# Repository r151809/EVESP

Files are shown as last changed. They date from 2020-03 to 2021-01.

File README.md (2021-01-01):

# EVESP
ESP32 (Lolin32) based EV charge controller
Implement charging controller according to SAE J1772 (https://en.wikipedia.org/wiki/SAE_J1772) and relay driver.

Project maturity: just schematics (no testing nor SW yet)!

Only fixed cables are supported (no PP support).

Recidual current (AC+DC) protection is planned with https://deltrixchargers.com/wp-content/uploads/2019/10/WA-DS-015-RCM14-03-Rev-B.pdf
https://www.stegen.com/nl/ev-producten/126-residual-current-sensor.html

Three relays, one for each phase. This is inteded for cases when there is unsymmetrical load in the house, and you still want to charge the car (maybe there is another car charging in one phase already). Another usecase is cars that go to sleep when not charged, and while sleeping they do not accept pre heat commands from the cloud. My take for that would be charging with single phase with 6A current, instead of not charging at all, full 3-phase charging only when you really want to charge. Changing the phases on the fly might not be supported by cars, but that is easy to overcome by stopping the charge before switching on/off any phases.

Misc features:
4 local LEDs
8 IO for external LEDs or buttons
1 up to 12 V LED output for lighting up the charging cable dummy socket (where you keep the cable when it's not connected to car)  

Many ideas (component selection) of the schematic are taken from https://github.com/SmartEVSE/smartevse and from http://www.analogevse.xyz/AnalogEVSE-en.html. 

PWM generation and Wifi connectivity is handled with LoLin32-board:
https://wiki.wemos.cc/products:lolin32:lolin32
It's discontinued already, but you can still find them from ebay.
Pinout is here: https://arduino-projekte.info/wemos-lolin32/

Security:
SW cannot enable relay drivers unless RCM is happy and CP is connected to some load. So the design should be safe in case of forced disconnect and any ground leakage.

Manufacturing of the first PCB patch was done by Itead.cc with files in EVESP.zip.

## Copying
Feel free to copy anything I have added to this project. If it is not too much to ask, please let me know what you are doing (it's not mandatory) :). Also any bug's would be nice to know.

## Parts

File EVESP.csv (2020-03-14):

Id | Designator | Kotelo | Lukumäärä | Merkintä | Supplier and ref
1 | C21,C20,C19,C23,C22,C18,C17,C16,C13,C11,C15,C14,C10,C9,C8 | C_0805_2012Metric_Pad1.15x1.40mm_HandSolder | 15 | 100n
2 | C2,C12 | C_0805_2012Metric_Pad1.15x1.40mm_HandSolder | 2 | 10u
3 | R30,R23,R17 | R_0805_2012Metric_Pad1.15x1.40mm_HandSolder | 3 | 100k
4 | D13,D12,D11,D5,D4,D3,D2,D1 | SOT-23 | 8 | BAT54S
5 | H6,H5,H4,H3 | MountingHole_4.3mm_M4 | 4 | MountingHole
6 | D10,D9,D8,D7 | LED_2010_5025Metric_Pad1.52x2.65mm_HandSolder | 4 | LED
7 | R22,R15 | R_0805_2012Metric_Pad1.15x1.40mm_HandSolder | 2 | 1M
8 | J12,J11,J10,J1 | TerminalBlock_bornier-2_P5.08mm | 4 | Screw_Terminal_01x02
9 | U4,U3,U2 | SMDIP-6_W7.62mm | 3 | MOC3063M
10 | U5,U1 | SOIC-8_3.9x4.9mm_P1.27mm | 2 | LM7332
11 | R21,R40 | R_0805_2012Metric_Pad1.15x1.40mm_HandSolder | 2 | 47k
12 | R20,R19,R16,R9,R49,R13,R8,R6,R38,R42,R41,R39,R12,R7,R5,R4,R3,R34,R24,R10,R11,R2,R1 | R_0805_2012Metric_Pad1.15x1.40mm_HandSolder | 23 | 10k
13 | R18 | R_0805_2012Metric_Pad1.15x1.40mm_HandSolder | 1 | 6k8
14 | Q3,Q2,Q1 | SOT-23 | 3 | BC847
15 | J2 | Wago_734-136_1x06_P3.50mm_Vertical | 1 | Screw_Terminal_01x06
16 | R50,R48,R47,R46 | R_1206_3216Metric_Pad1.42x1.75mm_HandSolder | 4 | 470R
17 | R45,R44,R43,R14,R25 | R_0805_2012Metric_Pad1.15x1.40mm_HandSolder | 5 | 1k
18 | J9,J8 | Wago_734-133_1x03_P3.50mm_Vertical | 2 | Screw_Terminal_01x03
19 | J7 | PinHeader_1x20_P2.54mm_Vertical | 1 | Conn_01x20_Male
20 | J6 | PinHeader_1x20_P2.54mm_Vertical | 1 | Conn_01x20_Female
21 | J5 | PinHeader_1x16_P2.54mm_Vertical | 1 | Conn_01x16_Female
22 | J4 | PinHeader_1x16_P2.54mm_Vertical | 1 | Conn_01x16_Male
23 | D6 | D_SMA_Handsoldering | 1 | SMAJ13CA-13-F
24 | R29,R28,R27,R26,R37,R36,R35 | R_0805_2012Metric_Pad1.15x1.40mm_HandSolder | 7 | 470R
25 | RV3,RV2,RV1 | RV_Disc_D15.5mm_W6.8mm_P7.5mm | 3 | V275LA20AP
26 | PS3,PS2 | Converter_ACDC_MeanWell_IRM-02-xx_THT | 2 | IRM-02-12
27 | PS1 | Converter_ACDC_MeanWell_IRM-02-xx_THT | 1 | IRM-02-3.3
28 | J3 | JST_EH_B4B-EH-A_1x04_P2.50mm_Vertical | 1 | Conn_01x04
29 | F1 | Fuseholder_Cylinder-5x20mm_Stelvio-Kontek_PTF78_Horizontal_Open | 1 | 1.25A
30 | C3 | R_0805_2012Metric_Pad1.15x1.40mm_HandSolder | 1 | DNI 100n
31 | C7,C6,C5 | C_Radial_D6.3mm_H11.0mm_P2.50mm | 3 | 47u
32 | C4 | C_0805_2012Metric_Pad1.15x1.40mm_HandSolder | 1 | 270p

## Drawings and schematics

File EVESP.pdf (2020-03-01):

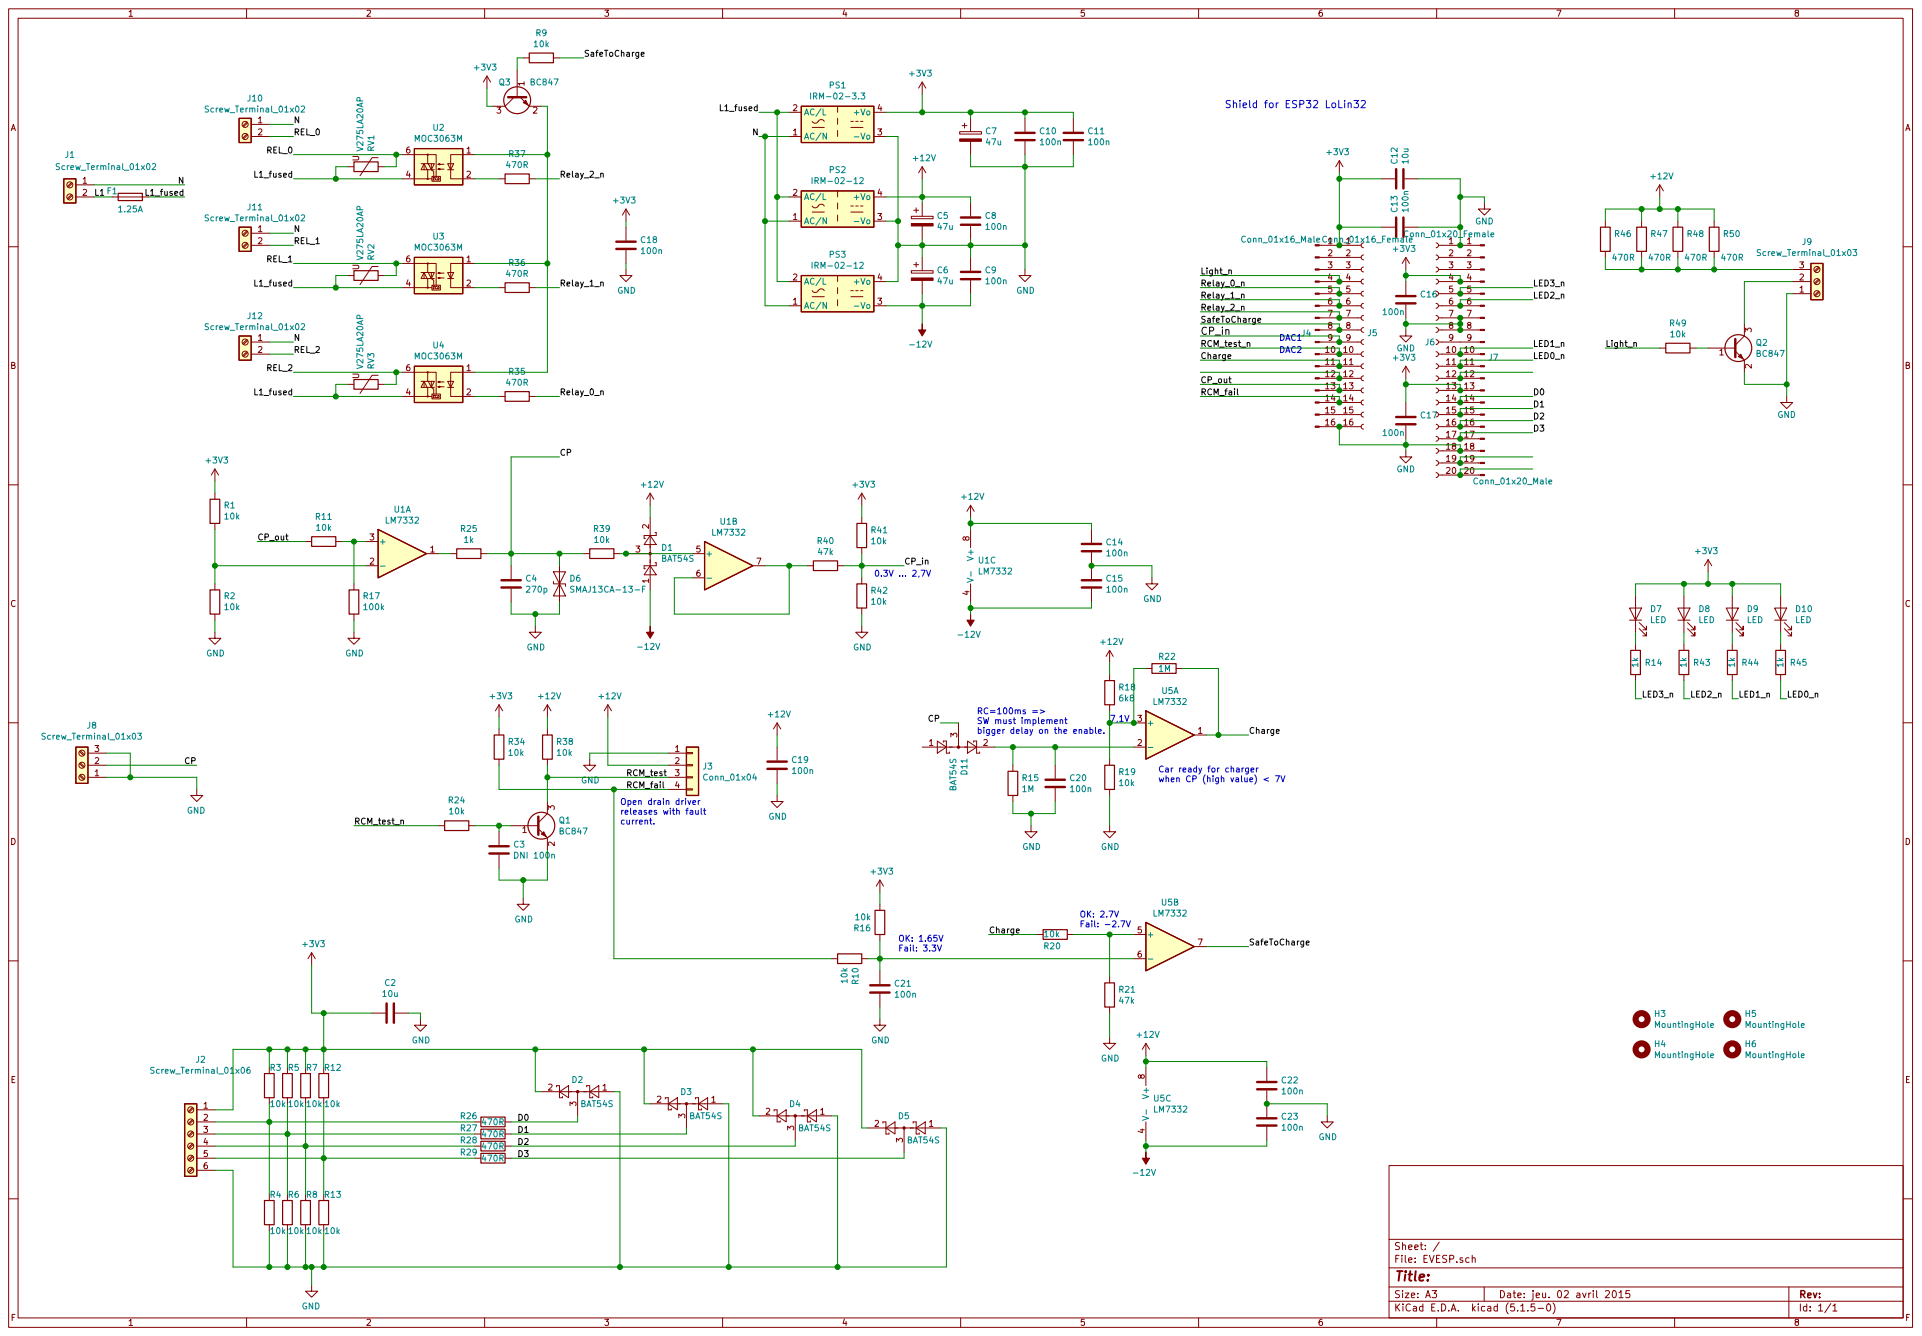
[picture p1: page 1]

Shield for ESP32 LoLin32 RC=100ms => SW must implement

DAC2 Car ready for charger

bigger delay on the enable.

when CP (high value) < 7V

Open drain driver releases with fault current.

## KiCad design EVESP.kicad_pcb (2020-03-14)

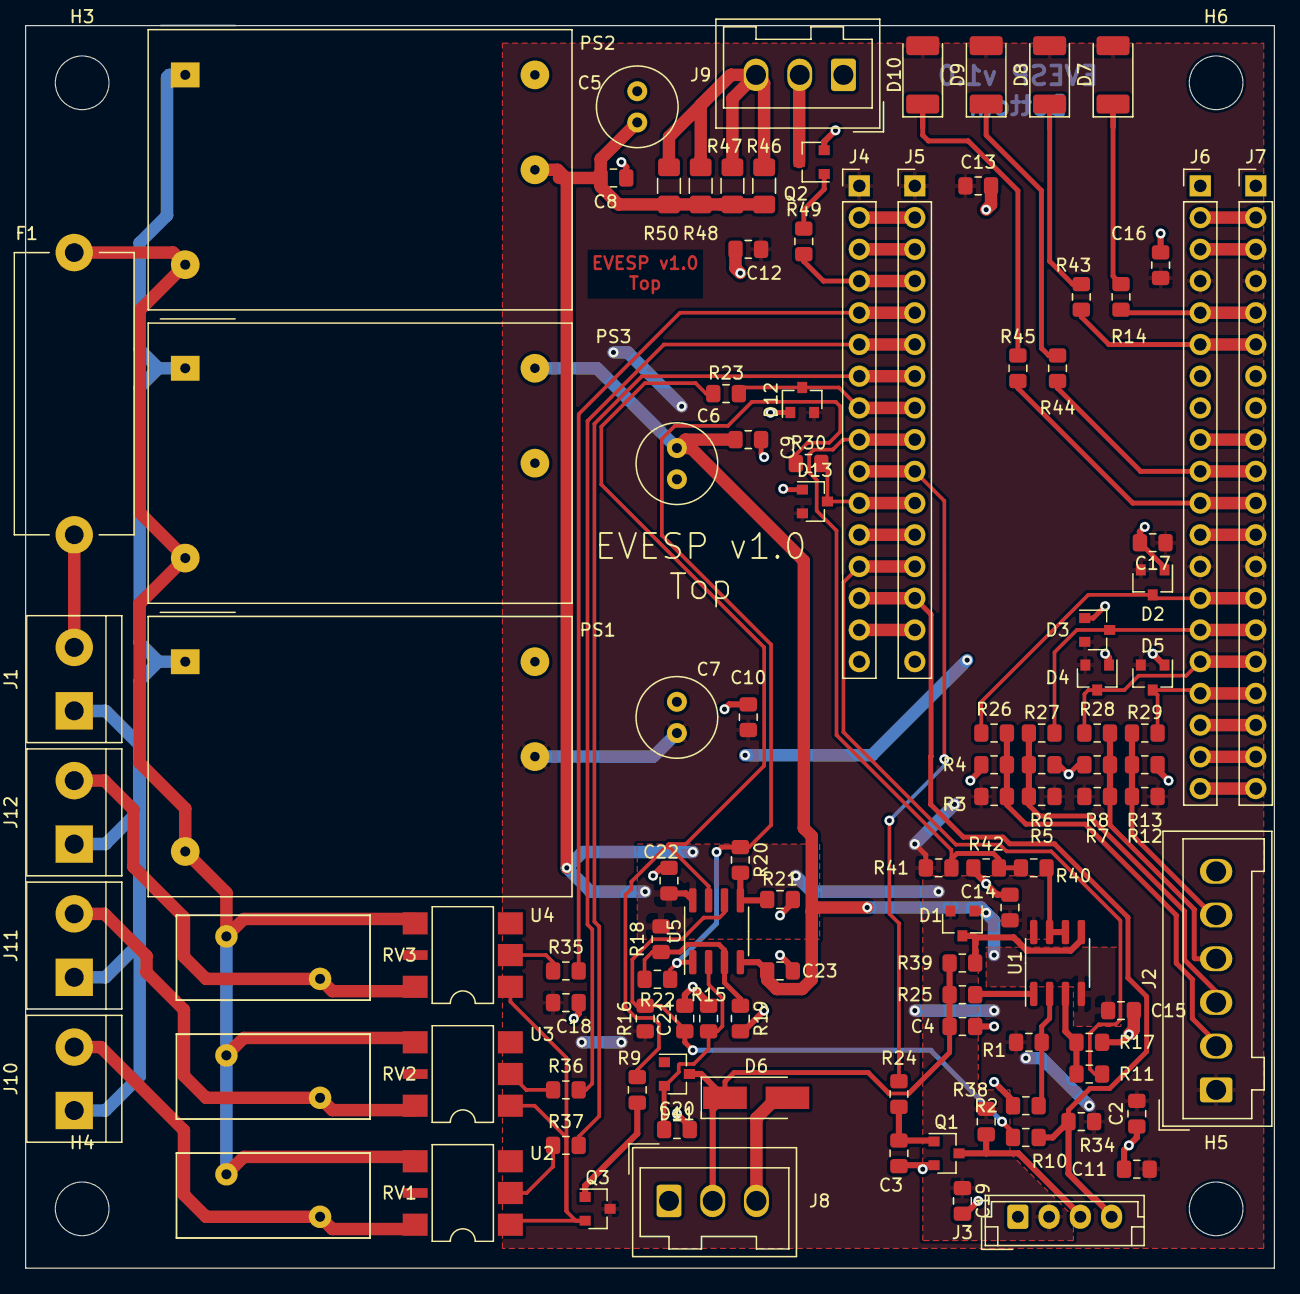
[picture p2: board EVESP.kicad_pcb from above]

Board: 2 copper layers, 100.0 x 99.5 mm, 113 parts (0 on the bottom side), 68 nets.

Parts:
C2, C12: 10u; C_0805_2012Metric_Pad1.15x1.40mm_HandSolder
C3: DNI 100n; R_0805_2012Metric_Pad1.15x1.40mm_HandSolder
C4: 270p; C_0805_2012Metric_Pad1.15x1.40mm_HandSolder
C5, C6, C7: 47u; C_Radial_D6.3mm_H11.0mm_P2.50mm
C8, C9, C10, C11, C13, C14, C15, C16, C17, C18, C19, C20, C21, C22, C23: 100n; C_0805_2012Metric_Pad1.15x1.40mm_HandSolder
D1, D2, D3, D4, D5, D11, D12, D13: BAT54S; SOT-23
D6: SMAJ13CA-13-F; D_SMA_Handsoldering
D7, D8, D9, D10: LED; LED_2010_5025Metric_Pad1.52x2.65mm_HandSolder
F1: 1.25A; Fuseholder_Cylinder-5x20mm_Stelvio-Kontek_PTF78_Horizontal_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
H3, H4, H5, H6: MountingHole; MountingHole_4.3mm_M4
J1, J10, J11, J12: Screw_Terminal_01x02; TerminalBlock_bornier-2_P5.08mm
J2: Screw_Terminal_01x06; Wago_734-136_1x06_P3.50mm_Vertical
J3: Conn_01x04; JST_EH_B4B-EH-A_1x04_P2.50mm_Vertical
J4: Conn_01x16_Male; PinHeader_1x16_P2.54mm_Vertical
J5: Conn_01x16_Female; PinHeader_1x16_P2.54mm_Vertical
J6: Conn_01x20_Female; PinHeader_1x20_P2.54mm_Vertical
J7: Conn_01x20_Male; PinHeader_1x20_P2.54mm_Vertical
J8, J9: Screw_Terminal_01x03; Wago_734-133_1x03_P3.50mm_Vertical
PS1: IRM-02-3.3; Converter_ACDC_MeanWell_IRM-02-xx_THT
PS2, PS3: IRM-02-12; Converter_ACDC_MeanWell_IRM-02-xx_THT
Q1, Q2, Q3: BC847; SOT-23
R1, R2, R3, R4, R5, R6, R7, R8, R9, R10, R11, R12, R13, R16, R19, R20, R24, R34, R38, R39, R41, R42, R49: 10k; R_0805_2012Metric_Pad1.15x1.40mm_HandSolder
R14, R25, R43, R44, R45: 1k; R_0805_2012Metric_Pad1.15x1.40mm_HandSolder
R15, R22: 1M; R_0805_2012Metric_Pad1.15x1.40mm_HandSolder
R17, R23, R30: 100k; R_0805_2012Metric_Pad1.15x1.40mm_HandSolder
R18: 6k8; R_0805_2012Metric_Pad1.15x1.40mm_HandSolder
R21, R40: 47k; R_0805_2012Metric_Pad1.15x1.40mm_HandSolder
R26, R27, R28, R29, R35, R36, R37: 470R; R_0805_2012Metric_Pad1.15x1.40mm_HandSolder
R46, R47, R48, R50: 470R; R_1206_3216Metric_Pad1.42x1.75mm_HandSolder
RV1, RV2, RV3: V275LA20AP; RV_Disc_D15.5mm_W6.8mm_P7.5mm
U1, U5: LM7332; SOIC-8_3.9x4.9mm_P1.27mm
U2, U3, U4: MOC3063M; SMDIP-6_W7.62mm

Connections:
+3V3: C2.2, C7.1, C10.1, C11.1, C12.1, C13.1, C16.1, C17.1, C18.1, D2.2, D3.2, D4.2, D5.2, D7.2, D8.2, D9.2, D10.2, D12.2, D13.2, J2.1, J4.1, J5.1, J6.4, J6.13, J7.4, J7.13, PS1.4, Q3.3, R1.2, R3.1, R5.1, R7.1, R12.1, R16.1, R34.1, R41.1
+12V: C5.1, C8.1, C14.1, C19.1, C22.1, D1.2, J3.2, PS2.4, R18.1, R38.1, R46.1, R47.1, R48.1, R50.1, U1.8, U5.8
-12V: C6.2, C9.2, C15.2, C23.2, D1.1, PS3.3, U1.4, U5.4
/CP: C4.1, D6.1, D11.3, J8.2, R25.1, R39.2
/CP_in: J4.9, J5.9, R40.1, R41.2, R42.1
/CP_out: J4.13, J5.13, R11.2
/Charge: R20.1, R22.1, R30.1, U5.1
/D0: D2.3, J6.14, J7.14, R26.2
/D1: D3.3, J6.15, J7.15, R27.2
/D2: D4.3, J6.16, J7.16, R28.2
/D3: D5.3, J6.17, J7.17, R29.2
/L1: F1.1, J1.2
/L1_fused: F1.2, PS1.2, PS2.2, PS3.2, RV1.2, RV2.2, RV3.2, U2.4, U3.4, U4.4
/LED0_n: J6.11, J7.11, R45.2
/LED1_n: J6.10, J7.10, R44.2
/LED2_n: J6.6, J7.6, R43.2
/LED3_n: J6.5, J7.5, R14.2
/Light_n: J4.4, J5.4, R49.2
/N: J1.1, J10.1, J11.1, J12.1, PS1.1, PS2.1, PS3.1
/RCM_fail: J3.4, J4.14, J5.14, R10.1, R34.2
/RCM_test: J3.3, Q1.3, R38.2
/RCM_test_n: J4.10, J5.10, R24.1
/REL_0: J10.2, RV1.1, U2.6
/REL_1: J11.2, RV2.1, U3.6
/REL_2: J12.2, RV3.1, U4.6
/Relay_0_n: J4.5, J5.5, R35.2
/Relay_1_n: J4.6, J5.6, R36.2
/Relay_2_n: J4.7, J5.7, R37.2
/SafeToCharge: R9.1, R23.1, U5.7
GND: C2.1, C3.2, C4.2, C5.2, C6.1, C7.2, C8.2, C9.1, C10.2, C11.2, C12.2, C13.2, C14.2, C15.1, C16.2, C17.2, C18.2, C19.2, C20.2, C21.2, C22.2, C23.1, D2.1, D3.1, D4.1, D5.1, D6.2, D12.1, D13.1, J2.6, J3.1, J4.16, J5.16, J6.1, J6.7, J6.8, J6.18, J7.1, J7.7, J7.8, J7.18, J8.1, J8.3, J9.1, PS1.3, PS2.3, PS3.4, Q1.2, Q2.2, R2.1, R4.2, R6.2, R8.2, R13.2, R15.2, R17.1, R19.2, R21.2, R42.2
unnamed: C3.1, Q1.1, R24.2
unnamed: C20.1, D11.2, R15.1, U5.2
unnamed: C21.1, R10.2, R16.2, U5.6
unnamed: D1.3, R39.1, U1.5
unnamed: D7.1, R14.1
unnamed: D8.1, R43.1
unnamed: D9.1, R44.1
unnamed: D10.1, R45.1
unnamed: D12.3, J4.8, J5.8, R23.2
unnamed: D13.3, J4.11, J5.11, R30.2
unnamed: J2.2, R3.2, R4.1, R26.1
unnamed: J2.3, R5.2, R6.1, R27.1
unnamed: J2.4, R7.2, R8.1, R28.1
unnamed: J2.5, R12.2, R13.1, R29.1
unnamed: J4.2, J5.2
unnamed: J4.3, J5.3
unnamed: J4.12, J5.12
unnamed: J4.15, J5.15
unnamed: J6.2, J7.2
unnamed: J6.3, J7.3
unnamed: J6.9, J7.9
unnamed: J6.12, J7.12
unnamed: J6.19, J7.19
unnamed: J6.20, J7.20
unnamed: J9.2, Q2.3
unnamed: J9.3, R46.2, R47.2, R48.2, R50.2
unnamed: Q2.1, R49.1
unnamed: Q3.1, R9.2
unnamed: Q3.2, U2.1, U3.1, U4.1
unnamed: R1.1, R2.2, U1.2
unnamed: R11.1, R17.2, U1.3
unnamed: R18.2, R19.1, R22.2, U5.3
unnamed: R20.2, R21.1, U5.5
unnamed: R25.2, U1.1
unnamed: R35.1, U4.2
unnamed: R36.1, U3.2
unnamed: R37.1, U2.2
unnamed: R40.2, U1.6, U1.7

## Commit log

2020-02-27 Initial version.
    [EVESP.kicad_pcb, EVESP.sch]
2020-02-27 Added PDF of the schematics.
2020-02-29 Only 4 external LEDs. Smaller layout.
    [EVESP.kicad_pcb, EVESP.sch]
2020-02-29 Added analog protection against disconnect and diode failure on car side.
    [EVESP.kicad_pcb, EVESP.sch]
2020-03-01 Added HW safety. No relay drive unless the CP is connected and RCM is happy.
    [EVESP.kicad_pcb, EVESP.sch]
2020-03-01 +12V connectivity fixed
    [EVESP.kicad_pcb]
2020-03-01 Layout shrink to <= 10cm x 10 cm
    [EVESP.kicad_pcb]
2020-03-01 Added edge prints. Added prints.
    [EVESP.kicad_pcb]
2020-03-01 Better +3V3 plane.
    [EVESP.kicad_pcb]
2020-03-01 Minor changes.
    [EVESP.sch]
2020-03-01 AC side changed for 2mm clearance.
    [EVESP.kicad_pcb, EVESP.sch]
2020-03-01 Added hysteresis to charge -signal. Schematic review changes fixed.
    [EVESP.kicad_pcb, EVESP.sch]
2020-03-01 Layout ready. PDF updated.
    [EVESP.kicad_pcb]
2020-03-01 Added gerber and drill files.
    [EVESP.kicad_pcb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]
2020-03-02 Fixed +-12V drive towards the ESP32 (added resistor and a diode).
    [EVESP.kicad_pcb, EVESP.sch]
2020-03-02 Gerbers generated: Fixed +-12V drive towards the ESP32 (added resistor and a diode).
    [EVESP.kicad_pcb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]
2020-03-02 Added single drill file with PTH's and NPTH's
    [EVESP.drl]
2020-03-02 Board cutting fine tuned to leave more clearance on right side connector before edge cut.. Added final production files as zip.
    [EVESP.kicad_pcb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]
2020-03-12 C2 decal name fixed (both work fine so just a style fix)
    [EVESP.sch]
2020-03-12 C19-21 decal name fixed (both work fine so just a style fix)
    [EVESP.sch]
2020-03-14 Capacitors now all use capacitor decal (some were using resistor decal).
    [EVESP.kicad_pcb]
2020-03-14 CSV version of BOM.
    [EVESP.csv]
2021-01-01 PCB's done.
2021-01-01 Fixed the first bug: reistor division in charge -net was inverted.
    [EVESP.sch]
